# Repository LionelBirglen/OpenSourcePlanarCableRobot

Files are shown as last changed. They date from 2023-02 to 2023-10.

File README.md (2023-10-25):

# Open-Source Planar Cable-Driven Robot

This repository shares all the required information to build and control a simple and low-cost planar cable-driven parallel robot with four actuators, from editable CAD files and programs to electrical circuitry. The robot can be carted and moved around easily. It can also be programmed and operated with an included teach pendant without a computer connected to the machine. Voltages and currents fed to the actuators can be acquired through a D-sub connector for measurements.

See:<br>
http://cctomm.ca/2023/CCToMM_M3_Symposium_paper_9.pdf<br>
for more information. Corresponding citation is:<br>
Design, Control, and Experiments of a Low-Cost Open-Source Planar Cable-Driven Parallel Robot" by Mikael Arslan and Lionel Birglen, 2023 CCToMM M3 Symposium, June 19-20, 2023.

Video demonstrations:<br>
https://www.youtube.com/watch?v=gsjz_0bn3mc<br>
https://www.youtube.com/watch?v=OgFYR7lME20<br>

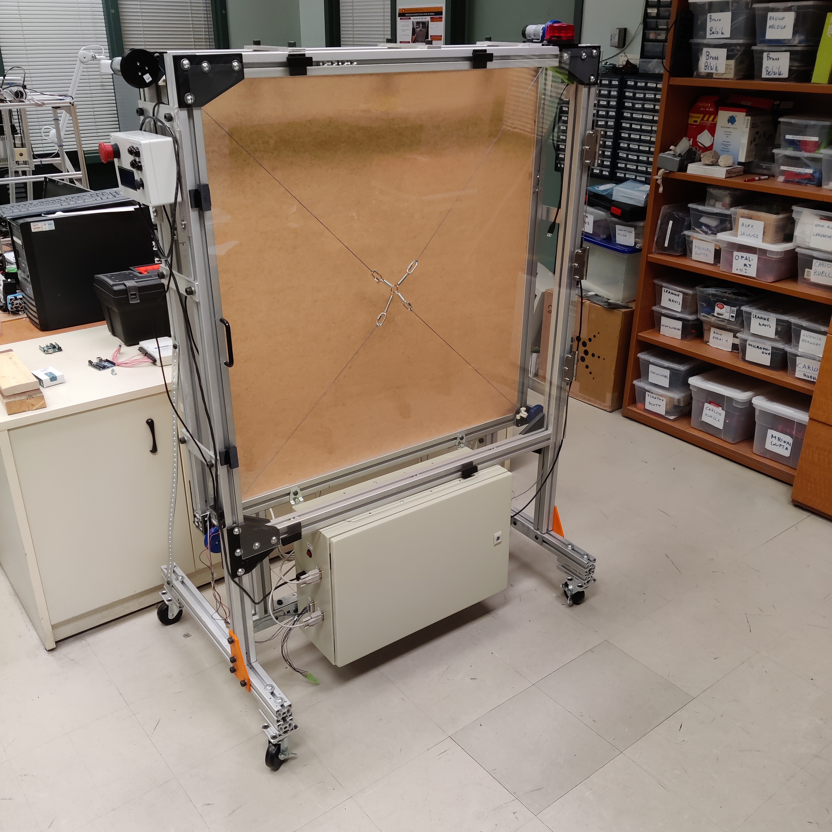
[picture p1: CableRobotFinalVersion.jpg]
Cable Robot Title


All files by Mikael Arslan and Lionel Birglen  <br />
Polytechnique Montreal<br />
2022-...

###  DISCLAIMER:
This hardware and software project is provided "as is", and at your own risk. Under no circumstances shall any author be liable for direct, indirect, special, incidental, or consequential damages resulting from the use, misuse, or inability to use this hardware/software, even if the authors have been advised of the possibility of such damages.

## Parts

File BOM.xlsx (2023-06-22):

PLANAR CDPR BILL OF MATERIALS
Designation | Manufacturer / Supplier | QTY | Unit | Unit Price | Total | Link / Comment
MECHANICAL STRUCTURE
Aluminum extrusions 45mm | Bosh-Rexroth | 14.1 | m | $35.36 | $498.55 | https://store.boschrexroth.com/Assembly-Technology/Basic-mechanic-elements/Profiles-and-accessories/Strut-profile/STRUT-PROFILE_3842553621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
Aluminum bars 3/8" x 1.5" | Hardware store | 1.6 | m | $26.00 | $41.60 | N/A
ABS for 3D printed parts | Amazon | 3.6 | kg | $22.87 | $82.35 | https://www.amazon.ca/AMZ3D-1-75mm-Black-Printer-Filament/dp/B01D999TVO
Caster wheels | Amazon | 4 |  | $6.05 | $24.19 | https://www.amazon.com/GBL-Casters-Castors-Furniture-Workbench/dp/B07KVM276F/
Polycarbonate Sheets: 1/8" (front) and 1/4" (back) thick, 1m square | Polyalto | 2 |  | $125.24 | $250.47 | https://www.polyalto.com/fr/catalogue/produits/polycarbonate-gp-tout-usage
Hinges | Amazon | 3 |  | $2.00 | $6.00 | https://www.amazon.com/Brushed-Interior-Corners-Residential-Hardware/dp/B09T3D2C62/
Springs box | Amazon | 1 |  | $12.01 | $12.01 | https://www.amazon.com/Neiko-50456A-Assortment-Compression-Extension/dp/B000K7M36W/
250lb cable | Amazon | 1 |  | $13.95 | $13.95 | https://www.amazon.com/emma-kites-Braided-Creative-Projects/dp/B01850OST0
Drop in T nuts | Aliexpress | 180 |  | $0.47 | $84.15 | https://www.aliexpress.com/item/4001249847405.html
M8 screws | Aliexpress | 180 |  | $0.31 | $55.44 | https://www.aliexpress.com/item/4000148454577.html
Door handle | Amazon | 1 |  | $6.50 | $6.50 | https://www.amazon.com/Uxcell-a11081400ux0074-Cabinet-Plastic-Rectangular/dp/B007VBT5CA/
Mini carabiner clip kit | Amazon | 1 |  | $8.99 | $8.99 | https://www.amazon.com/Stainless-Steel-Carabiner-Clip-Spring-Snap/dp/B08DTCM52N/
Eye hooks #3 kit | Aliexpress | 1 |  | $2.38 | $2.38 | https://www.aliexpress.com/item/1005002732256168.html
M3 screw kit | Amazon | 1 |  | $17.96 | $17.96 | https://www.amazon.com/VIGRUE-570PCS-Stainless-Assortment-Machine/dp/B08H24W42K/
ELECTRICAL HARDWARE
Panel mount usb connector | Amazon | 1 |  | $7.99 | $7.99 | https://www.amazon.com/ChenYang-Degree-Angled-Female-extension/dp/B00S5WJ5RO/
Electrical cabinet | Allied Electric | 1 |  | $103.46 | $103.46 | https://www.alliedelec.com/product/rs-pro-by-allied/7755328/70824480/
Electrical box (teach pendant) | Digikey | 1 |  | $7.60 | $7.60 | https://www.digikey.com/en/products/detail/bud-industries/PT-11557-G/387082
Push buttons | Digikey | 4 |  | $2.01 | $8.04 | https://www.digikey.com/en/products/detail/e-switch/PS1023ABLK/82862
Potentiometer Joystick | Digikey | 1 |  | $4.50 | $4.50 | https://www.digikey.com/en/products/detail/sparkfun-electronics/COM-09032/
680 ohm resistor | Digikey | 8 |  | $0.10 | $0.80 | https://www.digikey.com/en/products/detail/yageo/CFR-25JT-52-680R/9098651
1 kohm resistor | Digikey | 1 |  | $0.10 | $0.10 | https://www.digikey.com/en/products/detail/yageo/CFR-25JB-52-1K/96
100 nF capacitor | Digikey | 8 |  | $0.33 | $2.64 | https://www.digikey.com/en/products/detail/kemet/C320C104K3R5TA/12701287
22mF 25V capacitor | Digikey | 1 |  | $4.87 | $4.87 | https://www.digikey.com/en/products/detail/nichicon/LLS1E223MELB
LCD screen | Adafruit | 1 |  | $17.95 | $17.95 | https://www.adafruit.com/product/198
Barrier Blocks 2 positions | Digikey | 4 |  | $2.59 | $10.36 | https://www.digikey.com/en/products/detail/te-connectivity-amp-connectors/1546477-2/2284035
Barrier Blocks 4 positions | Digikey | 2 |  | $2.94 | $5.88 | https://www.digikey.com/en/products/detail/te-connectivity-amp-connectors/1546306-4/1277415
General purpose prototype boards | Digikey | 5 |  | $1.59 | $7.95 | https://www.digikey.com/en/products/detail/chip-quik-inc/SBBTH1508-1/5978279
Crimp Connectors | Amazon | 1 |  | $39.99 | $39.99 | https://www.amazon.com/haisstronica-Crimping-Connectors-HS-8327-Electrical/dp/B099W4FVRB/
Straight pin header (0.1" pitch) | Robotshop | 5 |  | $1.61 | $8.05 | https://www.robotshop.com/products/sfe-straight-pin-headers
Power entry module (IEC 320) | Digikey | 1 |  | $1.20 | $1.20 | https://www.digikey.com/en/products/detail/adam-tech/IEC-C-1-150/9830624
DB9 2m cable | Digikey | 4 |  | $5.20 | $20.80 | https://www.digikey.com/en/products/detail/cinch-connectivity-solutions/30-9506-99/3830292
DB-9 female connector | Digikey | 4 |  | $0.70 | $2.80 | https://www.digikey.com/en/products/detail/amphenol-cs-fci/DE09S064TLF/1001839
DB-9 male connector | Digikey | 4 |  | $0.72 | $2.88 | https://www.digikey.com/en/products/detail/amphenol-cs-fci/DE09P064TXLF/1001838
DB-15 | Digikey | 1 |  | $0.75 | $0.75 | https://www.digikey.com/en/products/detail/adam-tech/DA15-PR/9832244
D-sub backshells | Digikey | 4 |  | $0.78 | $3.12 | https://www.digikey.com/en/products/detail/assmann-wsw-components/AGP-09-G/1241839
Power switch on off with light | Digikey | 1 |  | $9.59 | $9.59 | https://www.digikey.com/en/products/detail/bulgin/H8553VBBA3-551W/2747894
Red Led | Digikey | 5 |  | $0.17 | $0.85 | https://www.digikey.com/en/products/detail/creeled-inc/C5SMF-RJF-CT0W0BB1/
CR2032 battery | Digikey | 1 |  | $0.48 | $0.48 | https://www.digikey.com/en/products/detail/murata-electronics/CR2032/9558425
12V Strobe Light | Amazon | 1 |  | $20.49 | $20.49 | https://www.amazon.com/12V-24V-Flashing-Magnetic-Straight-Forklift/dp/B07KF4HJ83/
Emergency Switch | Digikey | 1 |  | $57.77 | $57.77 | https://www.digikey.com/en/products/detail/omron-automation-and-safety/A22E-M-01/456041
Panduct wire duct | Allied Electric | 6 |  | $6.88 | $41.28 | https://www.alliedelec.com/product/panduit/f1x2lg6/70333454/
Power cord | Amazon | 1 |  | $6.75 | $6.75 | https://www.amazon.com/dp/B072BYGKZZ/
Nylon spacer kit | Amazon | 1 |  | $9.99 | $9.99 | https://www.amazon.com/Electrical-Spacers-Assortment-Threaded-Receptacle/dp/B0BKFYFXWR/
PG7 Cable Gland (10pcs) | Aliexpress | 1 |  | $1.17 | $1.17 | https://www.aliexpress.com/item/4000242432947.html
AWG 22 electrical wire (control signals) | Amazon | 1 |  | $16.98 | $16.98 | https://www.amazon.com/Silicone-Electrical-Conductor-Parallel-Flexible/dp/B07K9R9LBV/
AWG 18 electrical wire (motors) | Amazon | 1 |  | $12.98 | $12.98 | https://www.amazon.com/Silicone-Electrical-Conductor-Parallel-Flexible/dp/B07K9R9LBV/
MECHATRONIC ELEMENTS
DC Gearmotor 37Dx73L | Pololu | 4 |  | $51.95 | $207.80 | https://www.pololu.com/product/4755
L-Brackets | Pololu | 2 |  | $9.95 | $19.90 | https://www.pololu.com/product/1084
Universal Hubs | Pololu | 2 |  | $9.95 | $19.90 | https://www.pololu.com/product/1083
Current sensors ACS711EX | Pololu | 4 |  | $3.95 | $15.80 | https://www.pololu.com/product/2452
12V power supply | Digikey | 1 |  | $41.27 | $41.27 | https://www.digikey.com/en/products/detail/mean-well-usa-inc/LRS-350-12/7705030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
Roboclaw solo 30A | BasicMicro | 4 |  | $89.95 | $359.80 | https://www.basicmicro.com/Roboclaw-Solo-30A-34VDC-Motor-Controller_p_44.html
Arduino Mega | Robotshop | 1 |  | $48.40 | $48.40 | https://www.robotshop.com/products/arduino-mega-2560-microcontroller-rev3
Arduino pro mini | Robotshop | 1 |  | $10.95 | $10.95 | https://www.robotshop.com/products/arduino-pro-mini-328-5v-16mhz
VINT Hub (optional) | Phidgets | 1 |  | $30.00 | $30.00 | https://www.phidgets.com/?tier=3&catid=2&pcid=1&prodid=1202
MISC
Labels for the wiring | Amazon | 1 |  | $7.59 | $7.59 | https://www.amazon.com/Mr-Label-Inkjet-Printer-Support-Waterproof/dp/B01HB59G7O/
GRAND TOTAL |  |  |  |  | $2306.01
 |  |  |  |  | All prices exclude VAT, custom duties, and shipping
TOOL LIST
Screwdrivers
Drill with various size meshes
Soldering iron and tin
Miter saw (capable of aluminium cutting)
Allen keys
Electric tape
Heat shrink tubing
Crimping tool (if suggested connector kit not purchased)
Multimeter (optional, debugging)
Oscilloscope (optional, debugging)
Label maker (optional but strongly recommended)
AUTHORS
by Mikael Arslan and Lionel Birglen
Polytechnique Montreal
created: 2023-02-17
last update: 2023-06-22
Rev 1.02

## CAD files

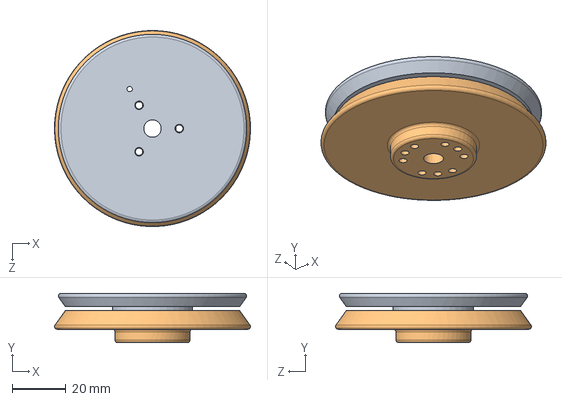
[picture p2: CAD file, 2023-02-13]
CAD/SpiralPulley/Assembly.SLDASM
73.1 x 18.4 x 73.1 mm
partB
partA

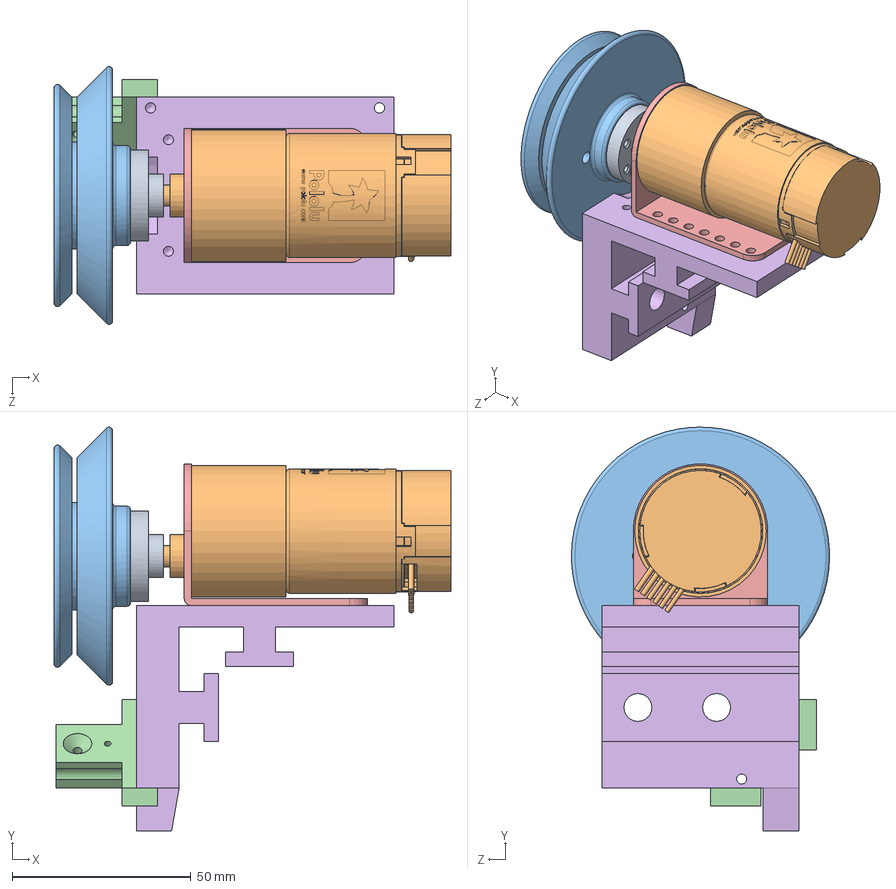
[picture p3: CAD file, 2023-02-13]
CAD/RobotMainFrame/ActuationUnit.SLDASM
111.0 x 112.9 x 72.1 mm
coupleur_poulie-moteur
moteur
poulie_originale
redirecteur
support_moteur
support_moteur_extrusion

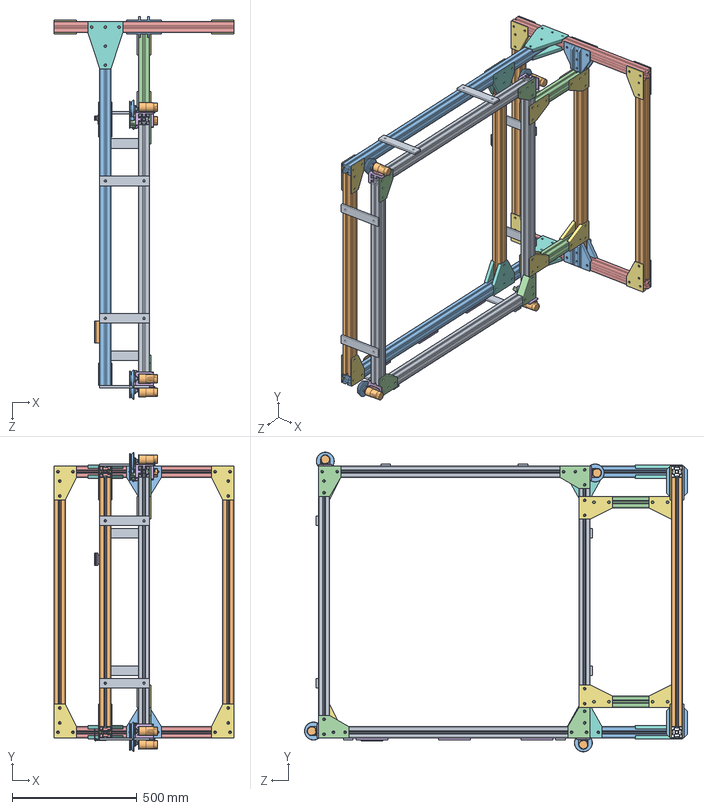
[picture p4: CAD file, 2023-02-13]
CAD/RobotMainFrame/CableRobotMainFrame.SLDASM
720.0 x 1201.8 x 1535.9 mm
extrusion_alu_45_1045 x 4
extrusion_alu_45_1000 x 5
extrusion_alu_45_1415 x 2
extrusion_alu_45_325 x 2
extrusion_alu_45_720 x 2
cale_charnière x 3
equerre_L_support_angle x 10
equerre_T_support_inferieur x 4
coupleur_poulie-moteur x 4
moteur x 4
poulie_originale x 4
redirecteur x 4
support_moteur x 4
support_moteur_extrusion x 4
equerre_L_support_angle_sym x 10
equerre_T_support_milieu x 4
barre_alu x 8
demi_charnière_porte_3.5in x 2
equerre_T_support_base x 4
equerre_L_support_angle_arriere x 4
support_aimant_plexi
support aimant cadre

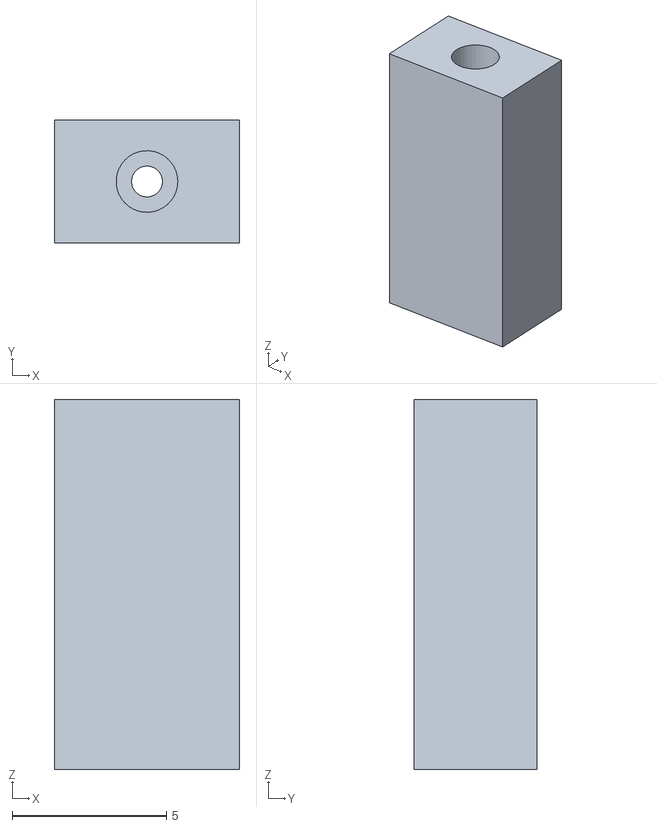
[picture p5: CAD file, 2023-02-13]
CAD/ElectricalCabinet/3DPrintedParts/standoff.STL
6.00 x 4.00 x 12.0

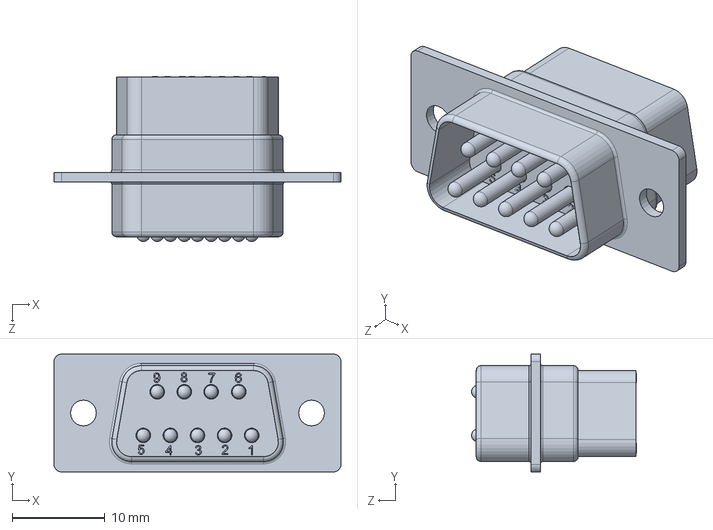
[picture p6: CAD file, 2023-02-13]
CAD/ElectricalCabinet/DB9_pins.SLDPRT
30.9 x 12.7 x 17.8 mm

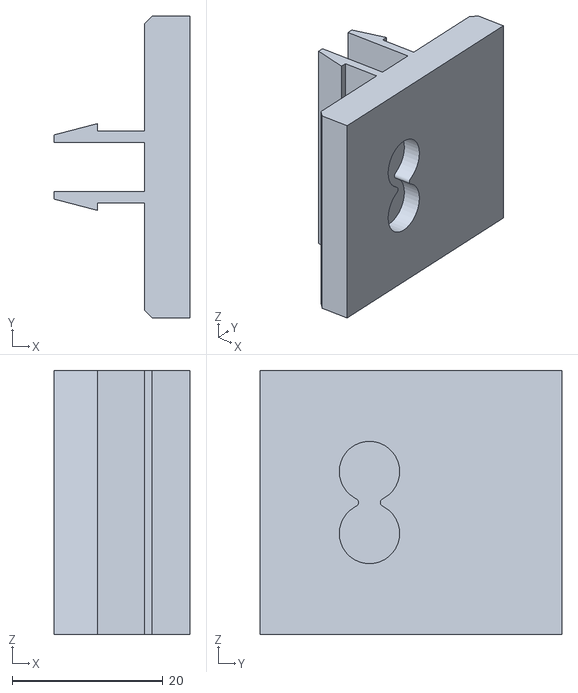
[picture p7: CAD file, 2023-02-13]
CAD/RobotMainFrame/3DPrintedParts/support aimant cadre_0.STL
18.0 x 40.0 x 35.0

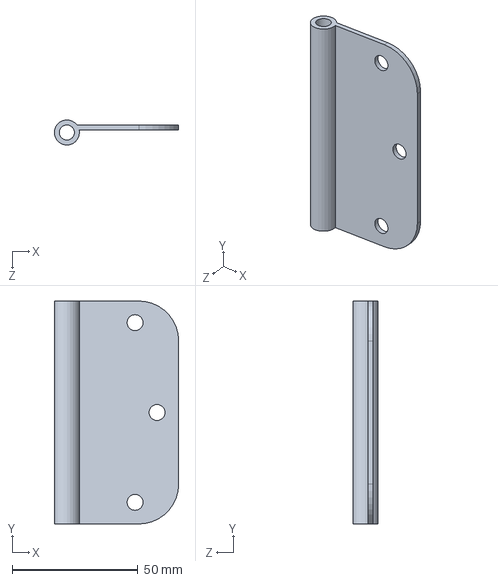
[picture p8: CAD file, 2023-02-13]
CAD/RobotMainFrame/demi_charnière_porte_3.5in.SLDPRT
49.4 x 88.6 x 9.98 mm

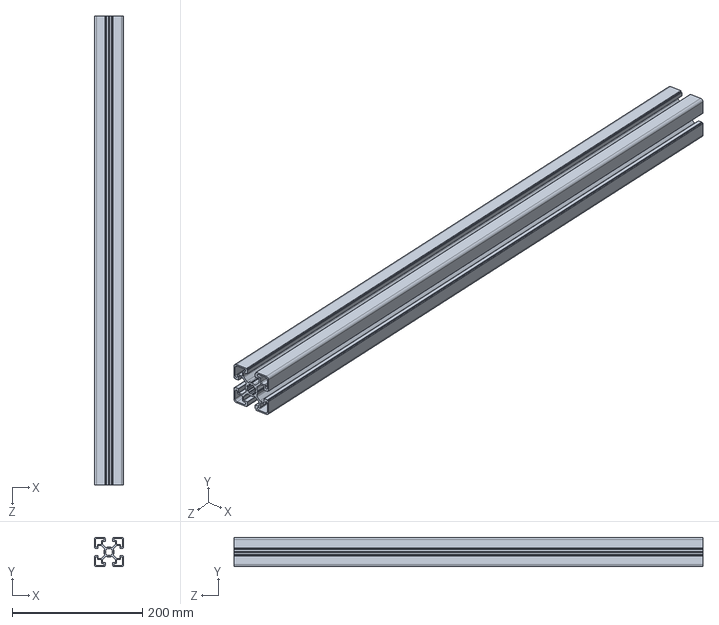
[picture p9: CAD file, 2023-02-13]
CAD/RobotMainFrame/extrusions/extrusion_alu_45_720.SLDPRT
45.0 x 45.0 x 720.0 mm

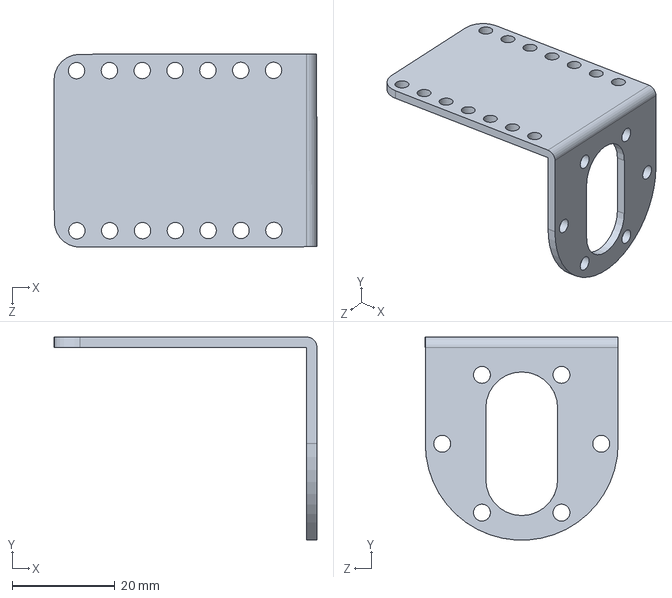
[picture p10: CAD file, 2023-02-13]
CAD/RobotMainFrame/pieces_bloc_moteur/support_moteur.SLDPRT
51.3 x 39.6 x 37.7 mm

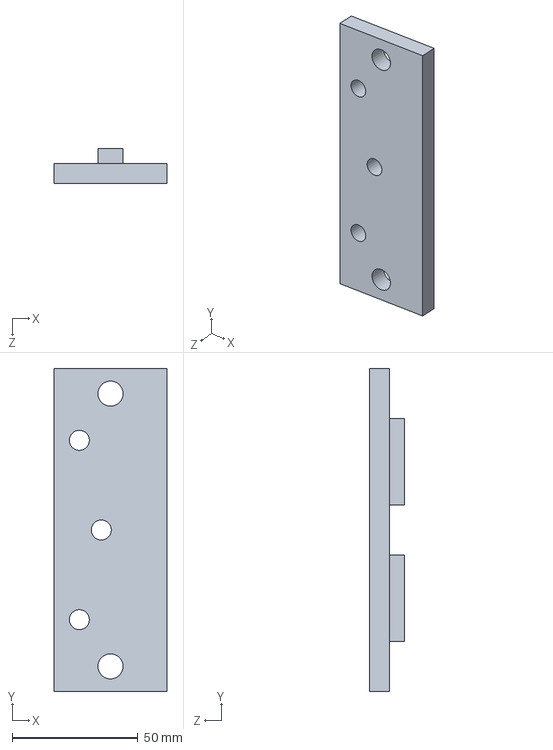
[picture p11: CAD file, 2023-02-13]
CAD/RobotMainFrame/pieces_imprimes/cale_charnière.SLDPRT
45.0 x 128.6 x 14.0 mm

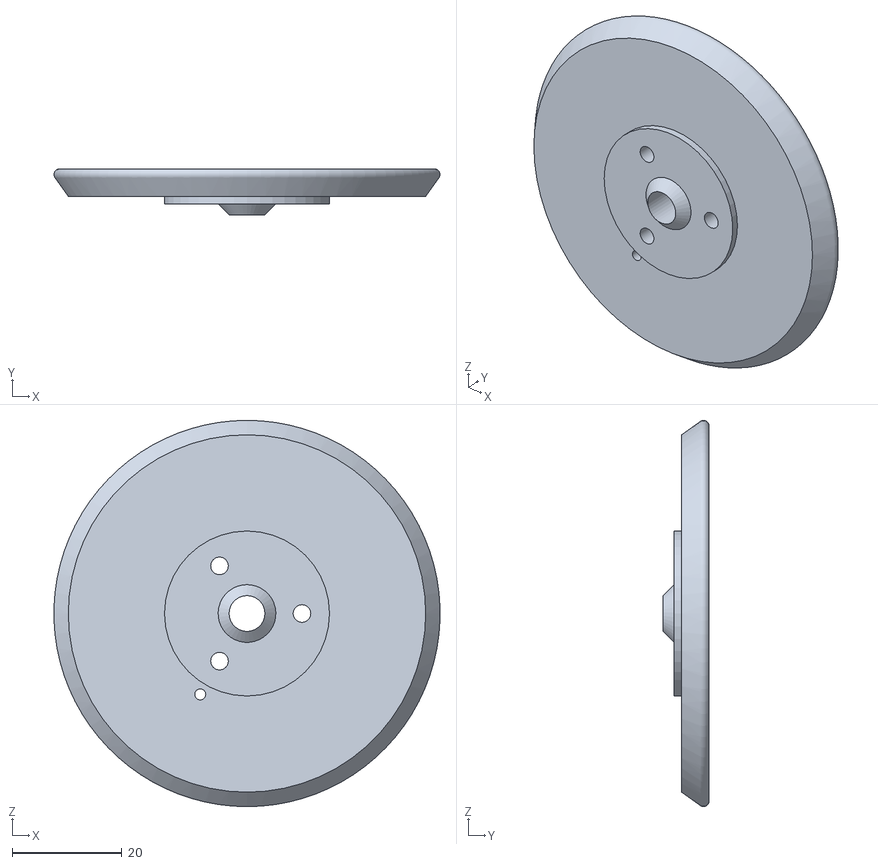
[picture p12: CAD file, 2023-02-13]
CAD/SpiralPulley/3DPrintedParts/partB.STL
70.2 x 8.40 x 70.3

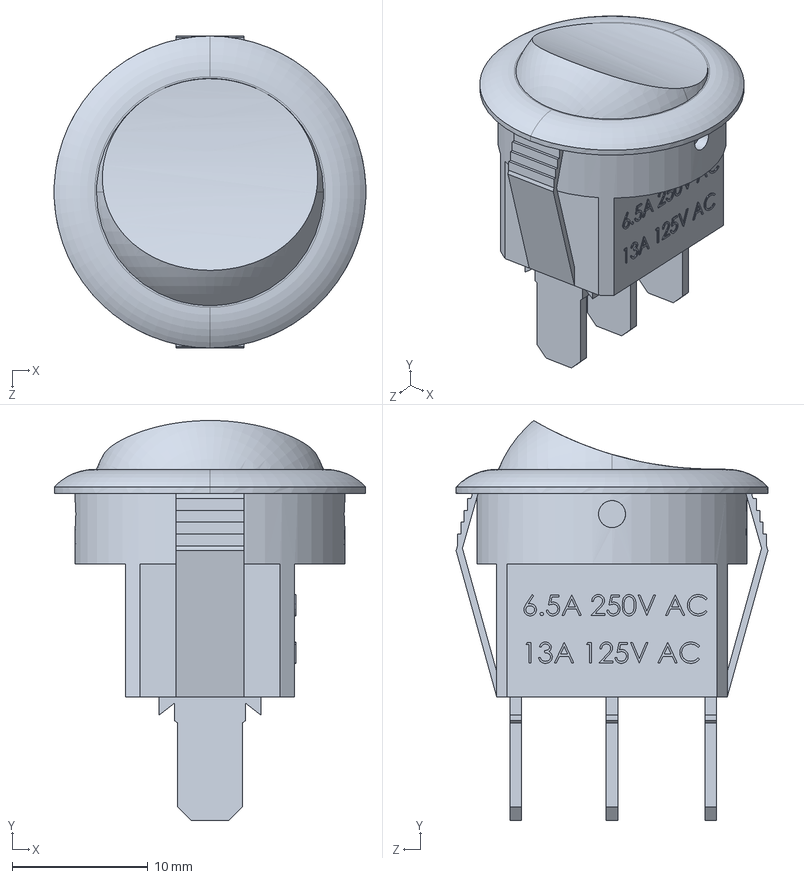
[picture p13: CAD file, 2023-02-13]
CAD/ElectricalCabinet/round_switch.SLDPRT
23.0 x 29.5 x 23.0 mm

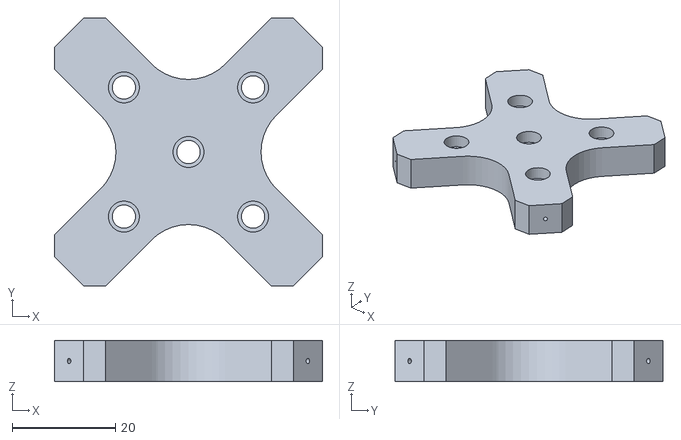
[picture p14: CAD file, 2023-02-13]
CAD/RobotMainFrame/3DPrintedParts/support_led_1.STL
51.9 x 51.9 x 8.00

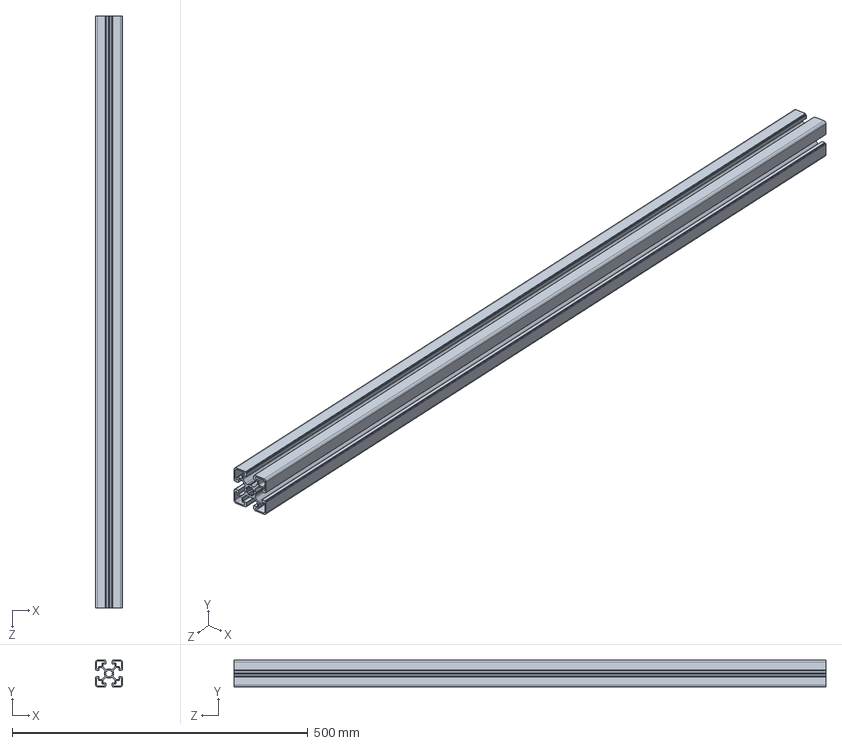
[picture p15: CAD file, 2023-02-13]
CAD/RobotMainFrame/extrusions/extrusion_alu_45_1000.SLDPRT
45.0 x 45.0 x 1000.0 mm

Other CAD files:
CAD/RobotMainFrame/pieces_bloc_moteur/coupleur_poulie-moteur.SLDPRT
CAD/RobotMainFrame/pieces_imprimes/Extrusion45Foot.stp
CAD/SpiralPulley/3DPrintedParts/partA.STL
CAD/SpiralPulley/partA.SLDPRT
CAD/ElectricalCabinet/Mean Well LRS-350 Power Supply.SLDPRT
CAD/ElectricalCabinet/arduino_mega.SLDPRT
CAD/ElectricalCabinet/backboard.SLDPRT
CAD/ElectricalCabinet/bonier_4.SLDPRT
CAD/ElectricalCabinet/bonier_6.SLDPRT
CAD/ElectricalCabinet/bouton.SLDPRT
CAD/ElectricalCabinet/current_sensor_ACS711EX.SLDPRT
CAD/ElectricalCabinet/d-sub-15.SLDPRT
CAD/ElectricalCabinet/roboclaw.SLDPRT
CAD/ElectricalCabinet/standoff_arduino.SLDPRT
CAD/ElectricalCabinet/wire_duct_250.SLDPRT
CAD/ElectricalCabinet/wire_duct_295.SLDPRT
CAD/ElectricalCabinet/wire_duct_440.SLDPRT
CAD/RobotMainFrame/3DPrintedParts/Extrusion45Foot v2_4.STL
CAD/RobotMainFrame/3DPrintedParts/cale_charnière_0.STL
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

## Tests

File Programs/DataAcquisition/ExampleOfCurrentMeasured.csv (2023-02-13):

2.300262451171875000e-03 -2.989200000004021973e-03 -4.746200000003586439e-03 4.461991999999941338e-01 -4.985159999999955183e-02
5.768537521362304688e-03 1.709499999999541942e-02 1.313899999999845747e-02 4.686289999999917466e-01 -3.416540000000911625e-02
1.411795616149902344e-02 4.626840000000020936e-02 3.556880000000317565e-02 5.000013999999939340e-01 -2.793000000006928829e-03
1.553654670715332031e-02 -4.095860000001261270e-02 2.208159999998882128e-02 4.731735999999944209e-01 -3.196640000000461335e-02
3.055453300476074219e-02 3.952479999999303217e-02 5.785199999999290910e-02 5.089439999999914033e-01 -7.337600000009603107e-03
3.854870796203613281e-02 -5.224680000000825331e-02 -5.840180000000261273e-02 3.992872000000022847e-01 -1.035072000000056835e-01
3.854870796203613281e-02 6.415359999999514784e-02 5.785199999999290910e-02 5.133419999999933037e-01 8.348599999995043319e-03
5.453991889953613281e-02 1.944059999999359079e-02 -5.620280000000521525e-02 4.127743999999953228e-01 -8.562200000000363964e-02
6.253337860107421875e-02 3.058219999999556293e-02 6.239659999999558337e-02 5.022003999999913315e-01 -4.992000000004326310e-03
7.054591178894042969e-02 3.754399999988944359e-03 1.997399999996485320e-03 4.618853999999987803e-01 -3.196640000000461335e-02
7.852053642272949219e-02 2.838319999999816545e-02 3.322319999999079343e-02 4.887131999999982934e-01 -9.536600000007000588e-03
7.852053642272949219e-02 6.195459999999775036e-02 3.776779999999346771e-02 5.000013999999939340e-01 -2.793000000006928829e-03
9.450960159301757812e-02 4.172379999999753508e-02 3.776779999999346771e-02 4.843151999999963930e-01 -1.408120000000967487e-02
9.450960159301757812e-02 6.415359999999514784e-02 7.573719999999495300e-02 5.200855999999933754e-01 2.183579999999518684e-02
1.105012893676757812e-01 4.626840000000020936e-02 2.428059999999332419e-02 4.708279999999962495e-01 -2.522280000001164701e-02
1.184952259063720703e-01 5.960899999999247356e-02 6.239659999999558337e-02 5.089439999999914033e-01 6.149599999997645838e-03
1.184952259063720703e-01 2.603759999999288866e-02 2.647959999999782710e-02 4.775715999999963213e-01 -2.522280000001164701e-02
1.344830989837646484e-01 4.846739999999050141e-02 4.671039999999093695e-02 5.043993999999958344e-01 -2.793000000006928829e-03
1.424777507781982422e-01 3.058219999999556293e-02 2.882519999998889304e-02 4.731735999999944209e-01 -3.856340000000391122e-02
1.505122184753417969e-01 6.195459999999775036e-02 6.459559999999298086e-02 5.000013999999939340e-01 3.950599999993142930e-03
1.505122184753417969e-01 3.058219999999556293e-02 2.647959999999782710e-02 4.843151999999963930e-01 -2.522280000001164701e-02
1.664774417877197266e-01 6.855159999999704823e-02 6.239659999999558337e-02 5.089439999999914033e-01 1.289319999999061217e-02
1.744587421417236328e-01 5.953399999993447267e-03 2.882519999998889304e-02 4.753725999999918184e-01 -3.196640000000461335e-02
1.744587421417236328e-01 5.301199999999317569e-02 6.005099999999741200e-02 5.065984000000003373e-01 3.950599999993142930e-03
1.904482841491699219e-01 -5.188200000008524881e-03 3.102419999999339595e-02 4.731735999999944209e-01 -2.742180000000193907e-02
1.984767913818359375e-01 7.089719999999521960e-02 5.110839999999283734e-02 4.976557999999957627e-01 -4.992000000004326310e-03
2.064363956451416016e-01 -5.188200000008524881e-03 1.313899999999845747e-02 4.574873999999897745e-01 -3.856340000000391122e-02
2.064363956451416016e-01 6.195459999999775036e-02 5.785199999999290910e-02 5.022003999999913315e-01 -2.793000000006928829e-03
2.224295139312744141e-01 -3.436160000000620940e-02 -3.482000000016860497e-04 4.350575999999921617e-01 -4.310800000000658549e-02
2.224295139312744141e-01 7.089719999999521960e-02 6.005099999999741200e-02 5.089439999999914033e-01 1.054759999999244080e-02
2.384200096130371094e-01 1.709499999999541942e-02 6.395399999998385709e-03 4.461991999999941338e-01 -5.879420000000412649e-02
2.464241981506347656e-01 4.406939999999570645e-02 4.671039999999093695e-02 5.000013999999939340e-01 -4.992000000004326310e-03
2.544059753417968750e-01 1.489599999999091651e-02 -6.968999999999825334e-02 3.948891999999932789e-01 -9.001999999999843460e-02
2.623970508575439453e-01 4.406939999999570645e-02 5.565299999998840619e-02 5.089439999999914033e-01 1.604999999994971560e-03
2.704010009765625000e-01 5.066639999999500432e-02 2.882519999998889304e-02 4.372565999999895592e-01 -5.644859999999884970e-02
2.783887386322021484e-01 1.709499999999541942e-02 4.216579999999536810e-02 4.843151999999963930e-01 -1.628020000000707235e-02
2.864050865173339844e-01 5.960899999999247356e-02 3.556880000000317565e-02 4.954567999999983652e-01 -1.035072000000056835e-01
2.864050865173339844e-01 2.603759999999288866e-02 5.110839999999283734e-02 4.976557999999957627e-01 -4.992000000004326310e-03
2.944121360778808594e-01 5.960899999999247356e-02 4.451140000000064489e-02 5.022003999999913315e-01 -5.940000000024259208e-04
3.063070774078369141e-01 -7.672900000000248966e-02 -8.757520000000029725e-02 3.768573999999975666e-01 -1.213924000000077275e-01
3.086130619049072266e-01 3.754399999988944359e-03 8.594399999995783190e-03 4.552883999999923770e-01 -4.310800000000658549e-02
3.106274604797363281e-01 1.489599999999091651e-02 2.428059999999332419e-02 4.708279999999962495e-01 -2.962079999999933655e-02
3.186266422271728516e-01 5.960899999999247356e-02 5.565299999998840619e-02 5.089439999999914033e-01 1.289319999999061217e-02
3.186266422271728516e-01 2.838319999999816545e-02 2.208159999998882128e-02 4.731735999999944209e-01 -2.302380000000714411e-02
3.346164226531982422e-01 4.626840000000020936e-02 4.451140000000064489e-02 4.932577999999938623e-01 -5.940000000024259208e-04
3.426268100738525391e-01 2.838319999999816545e-02 2.882519999998889304e-02 4.775715999999963213e-01 -2.522280000001164701e-02
3.426268100738525391e-01 5.960899999999247356e-02 6.005099999999741200e-02 5.065984000000003373e-01 1.729119999999961799e-02
3.586006164550781250e-01 2.383859999999549117e-02 2.428059999999332419e-02 4.664299999999943491e-01 -2.962079999999933655e-02
3.665955066680908203e-01 5.960899999999247356e-02 6.679459999999037834e-02 5.089439999999914033e-01 6.149599999997645838e-03
3.745942115783691406e-01 2.163959999999098827e-02 2.647959999999782710e-02 4.731735999999944209e-01 -2.742180000000193907e-02
3.825850486755371094e-01 6.195459999999775036e-02 6.459559999999298086e-02 5.111429999999959062e-01 1.509219999999511508e-02
3.825850486755371094e-01 -8.567160000000706432e-02 -1.054604000000023412e-01 3.567731999999910197e-01 -1.438222000000053402e-01
3.985764980316162109e-01 3.754399999988944359e-03 1.093999999999395456e-02 4.618853999999987803e-01 -4.310800000000658549e-02
3.985764980316162109e-01 -7.672900000000248966e-02 -9.431880000000747444e-02 3.702603999999982687e-01 -1.347329999999999917e-01
4.145622253417968750e-01 -2.761800000000613764e-02 -3.157400000000309959e-02 4.149733999999998257e-01 -8.342299999999913673e-02
4.225575923919677734e-01 -8.567160000000706432e-02 -1.009158000000067723e-01 3.523751999999962248e-01 -1.438222000000053402e-01
4.225575923919677734e-01 3.512679999999823721e-02 3.322319999999079343e-02 4.775715999999963213e-01 -1.847919999999736440e-02
4.385488033294677734e-01 -7.672900000000248966e-02 -1.032614000000049437e-01 3.567731999999910197e-01 -1.347329999999999917e-01
4.465403556823730469e-01 3.278119999999296041e-02 2.882519999998889304e-02 4.843151999999963930e-01 -2.522280000001164701e-02
4.545538425445556641e-01 -5.188200000008524881e-03 -6.074740000000078410e-02 3.903445999999977101e-01 -8.107740000000096536e-02
4.625315666198730469e-01 4.846739999999050141e-02 5.345399999999811413e-02 5.043993999999958344e-01 1.604999999994971560e-03
4.625315666198730469e-01 4.406939999999570645e-02 -4.051660000000767425e-02 4.239159999999972950e-01 -1.168478000000050532e-01
4.705355167388916016e-01 4.406939999999570645e-02 6.005099999999741200e-02 5.043993999999958344e-01 1.054759999999244080e-02
4.865350723266601562e-01 1.489599999999091651e-02 1.533799999999585495e-02 4.708279999999962495e-01 -2.742180000000193907e-02
4.945104122161865234e-01 3.952479999999303217e-02 5.110839999999283734e-02 4.932577999999938623e-01 3.950599999993142930e-03
5.025124549865722656e-01 7.309619999999972251e-02 6.459559999999298086e-02 5.133419999999933037e-01 2.623379999999708723e-02
5.104999542236328125e-01 3.058219999999556293e-02 4.216579999999536810e-02 4.865141999999937905e-01 -7.337600000009603107e-03
5.184977054595947266e-01 6.635259999999254532e-02 5.110839999999283734e-02 4.976557999999957627e-01 -5.940000000024259208e-04
5.264906883239746094e-01 2.163959999999098827e-02 4.216579999999536810e-02 4.797705999999937188e-01 -1.408120000000967487e-02
5.345206260681152344e-01 5.740999999999507608e-02 5.565299999998840619e-02 4.954567999999983652e-01 -4.992000000004326310e-03
5.425224304199218750e-01 3.512679999999823721e-02 3.322319999999079343e-02 4.686289999999917466e-01 -2.522280000001164701e-02
5.475902557373046875e-01 3.058219999999556293e-02 1.533799999999585495e-02 4.731735999999944209e-01 -3.196640000000461335e-02
5.486729145050048828e-01 2.838319999999816545e-02 2.208159999998882128e-02 4.775715999999963213e-01 -2.962079999999933655e-02
5.497503280639648438e-01 3.952479999999303217e-02 3.322319999999079343e-02 4.753725999999918184e-01 -2.742180000000193907e-02
5.517749786376953125e-01 3.732579999999563469e-02 3.556880000000317565e-02 4.932577999999938623e-01 -1.408120000000967487e-02
5.528295040130615234e-01 3.732579999999563469e-02 3.776779999999346771e-02 4.797705999999937188e-01 -1.628020000000707235e-02
5.538613796234130859e-01 -3.201600000000803803e-02 -3.391960000000127096e-02 4.239159999999972950e-01 -1.235914000000051249e-01
5.559298992156982422e-01 -8.127360000000516393e-02 -9.431880000000747444e-02 3.613177999999936940e-01 -1.303350000000051967e-01
5.570199489593505859e-01 -7.453000000000509218e-02 -7.408800000000725916e-02 3.679147999999929919e-01 -1.281360000000006938e-01
5.580401420593261719e-01 -2.527240000000086084e-02 -2.483040000000302783e-02 4.014861999999925768e-01 -9.676360000000561179e-02
5.590980052947998047e-01 -5.224680000000825331e-02 -5.840180000000261273e-02 3.613177999999936940e-01 -1.392776000000026659e-01
5.603177547454833984e-01 -8.127360000000516393e-02 -7.628700000000465664e-02 3.857999999999950358e-01 -1.079052000000004785e-01
5.623862743377685547e-01 -3.875960000000810979e-02 -5.180480000000331486e-02 4.440001999999967364e-01 -4.530699999999687755e-02
5.623862743377685547e-01 -2.989200000004021973e-03 3.322319999999079343e-02 4.797705999999937188e-01 -2.522280000001164701e-02
5.634076595306396484e-01 3.952479999999303217e-02 3.322319999999079343e-02 4.753725999999918184e-01 -2.522280000001164701e-02
5.644259452819824219e-01 3.952479999999303217e-02 3.102419999999339595e-02 4.708279999999962495e-01 -2.522280000001164701e-02
5.664587020874023438e-01 2.838319999999816545e-02 2.882519999998889304e-02 4.642309999999898462e-01 -2.522280000001164701e-02
5.674738883972167969e-01 3.278119999999296041e-02 1.988259999999142380e-02 4.775715999999963213e-01 -1.628020000000707235e-02
5.685033798217773438e-01 3.058219999999556293e-02 2.647959999999782710e-02 4.731735999999944209e-01 -1.408120000000967487e-02
5.695266723632812500e-01 3.512679999999823721e-02 -6.945200000008089347e-03 4.440001999999967364e-01 -5.879420000000412649e-02
5.705511569976806641e-01 -7.013200000000319179e-02 -7.628700000000465664e-02 3.857999999999950358e-01 -1.146488000000076557e-01
5.716249942779541016e-01 -8.567160000000706432e-02 -1.054604000000023412e-01 3.567731999999910197e-01 -1.347329999999999917e-01
5.726549625396728516e-01 -8.347260000000256142e-02 -1.054604000000023412e-01 3.523751999999962248e-01 -1.414766000000071688e-01
5.727074146270751953e-01 -6.338840000000312003e-02 -7.408800000000725916e-02 3.702603999999982687e-01 -1.213924000000077275e-01
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

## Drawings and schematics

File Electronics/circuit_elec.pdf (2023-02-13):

NKC electronics... | 2.2k

Terminal block...

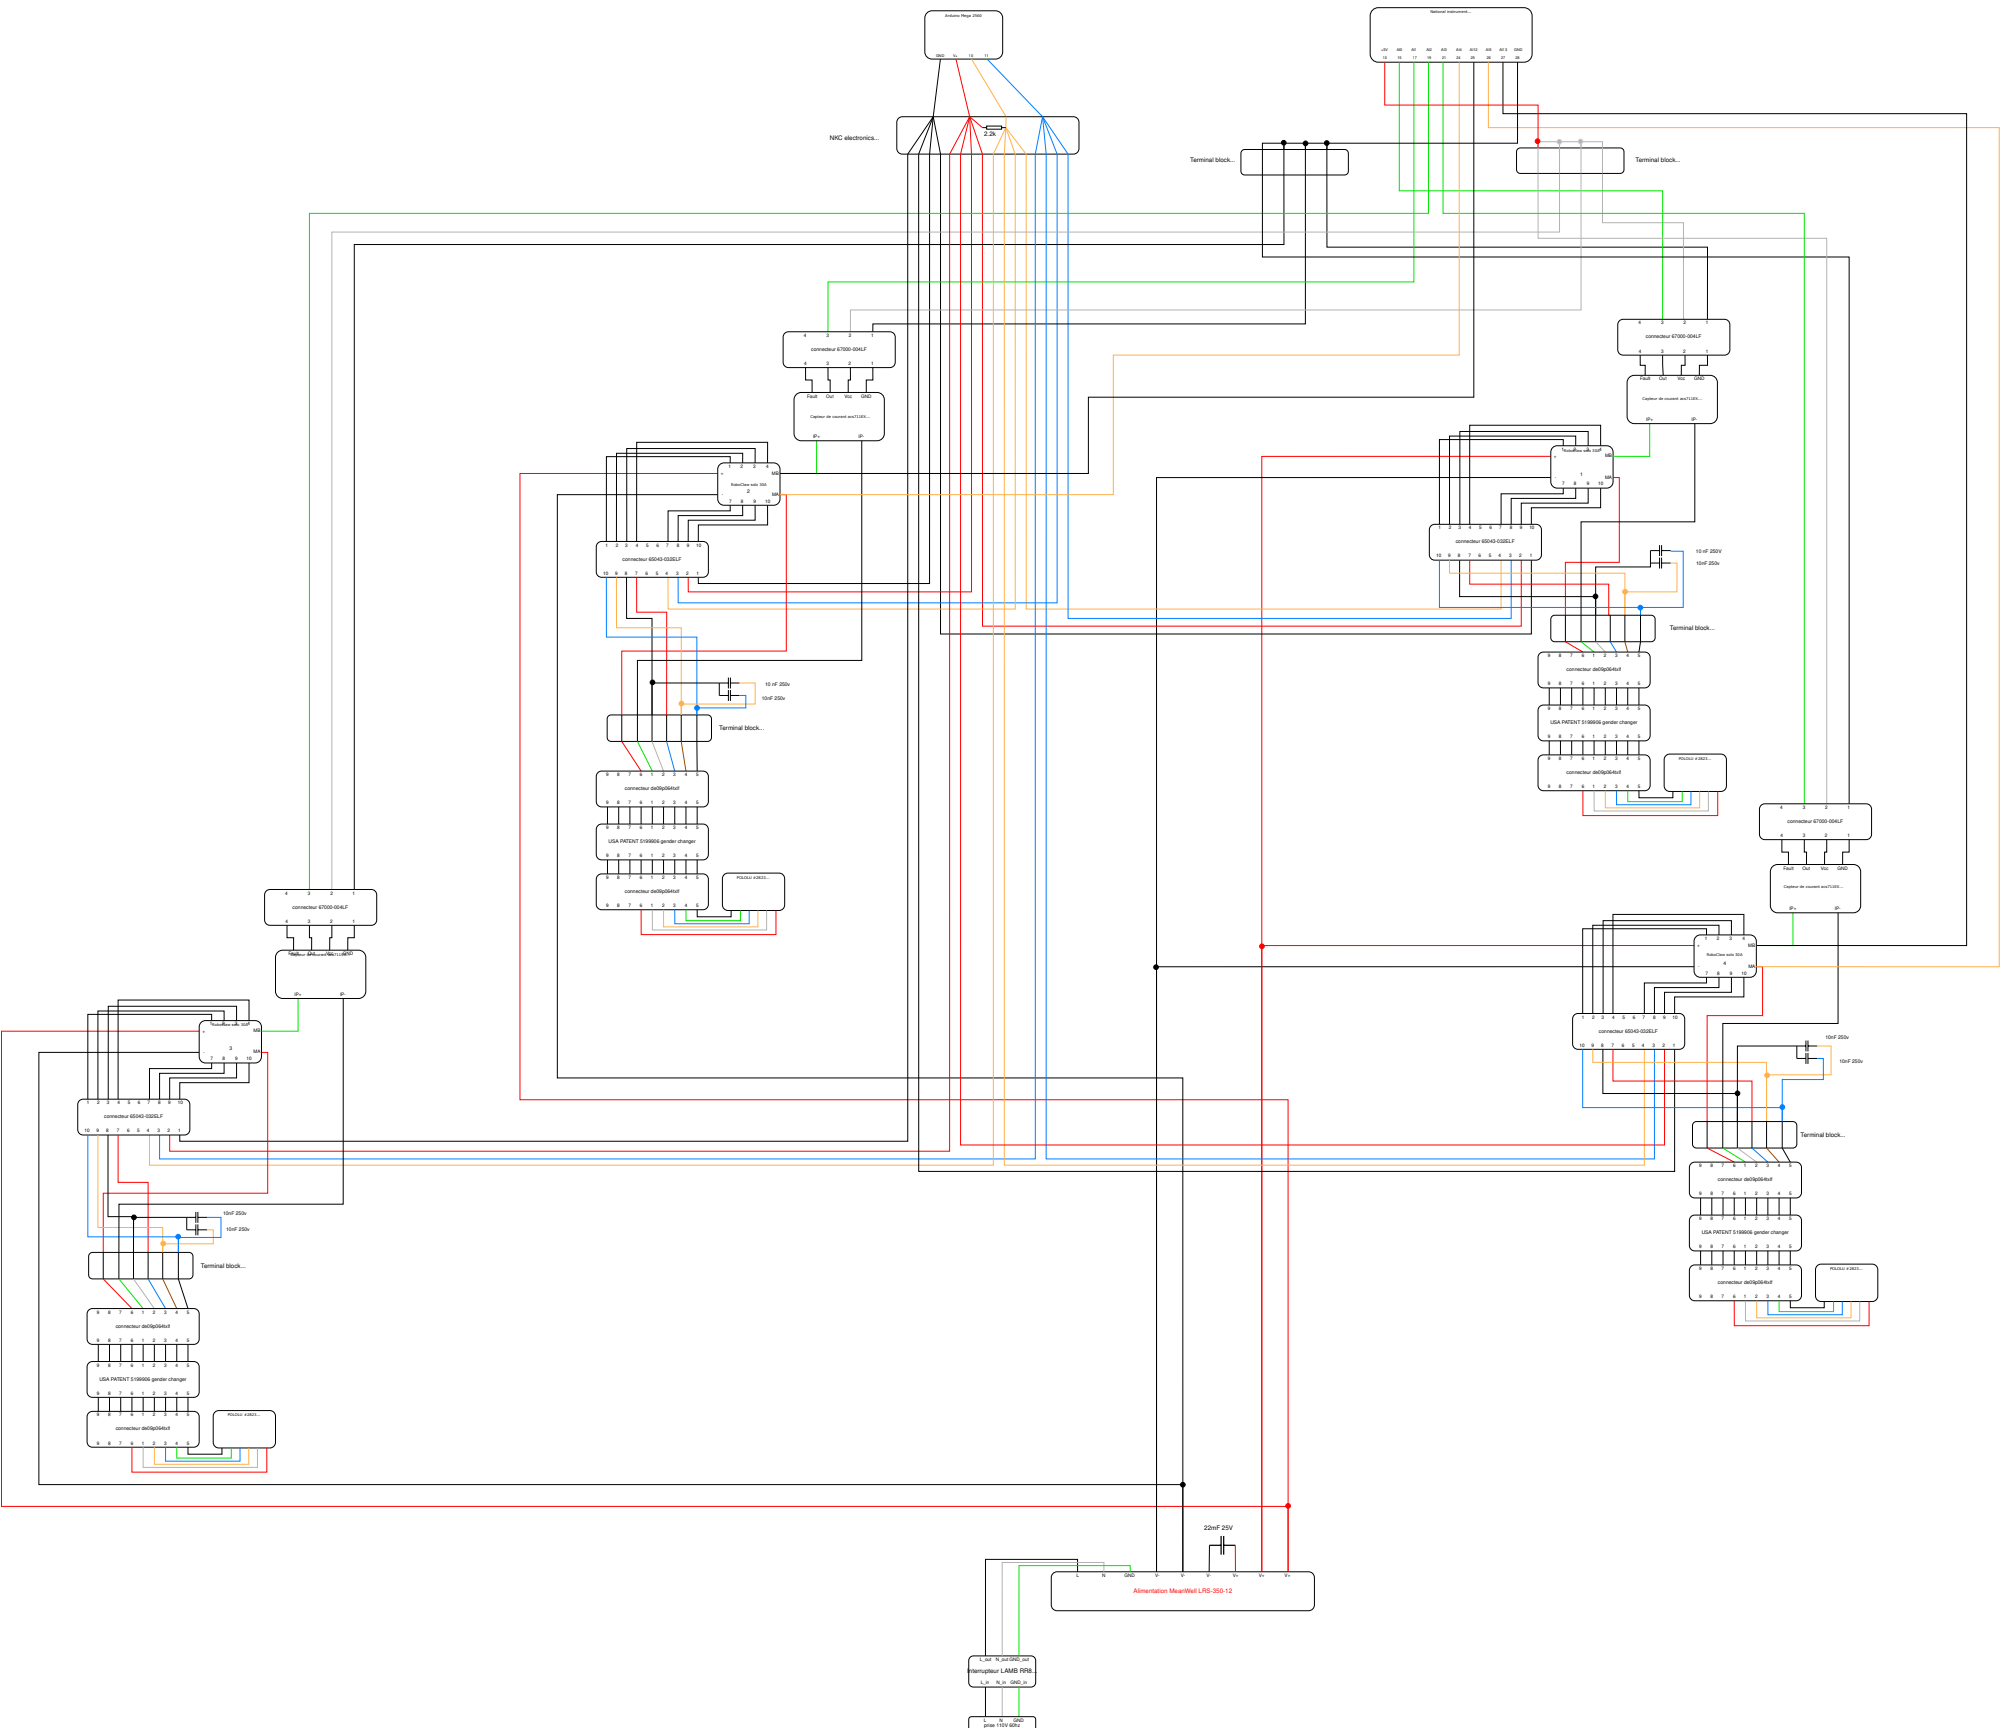
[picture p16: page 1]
Interrupteur LAMB RR8...; L_out; GND_outN_out; GND_inN_in; National instrument...; GND; Arduino Mega 2560; GNDN; prise 110V 60hz; RoboClaw solo 30A; connecteur 65043-032ELF; connecteur 67000-004LF; Fault; VccOut; Terminal block...; POLOLU #2823...; connecteur de09p064txlf

Capteur de courant acs711EX...

USA PATENT 5199906 gender changer

Alimentation MeanWell LRS-350-12

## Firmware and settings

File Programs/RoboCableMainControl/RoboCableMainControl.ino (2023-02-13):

//Includes required to use Roboclaw library
#include <SoftwareSerial.h>
#include "RoboClaw.h"
#include "menu_funcs.h"
#include "variables.h"
#include "com.h"

/*
int step_counter = 0;
int char_step_counter;
char step_msg[50];
int32_t step_mot[4] = {0,0,0,0};
bool read_step = false;

bool decode_step_msg() {

  if (Serial.available()) { // if there is a char

    char step_ch = Serial.read(); // read

    if(step_ch == 'g'){
      Serial.println("zero");
      go_to_zero();
    } 

    if (read_step) { // if we are currently reading a message, add the char to the message
      step_msg[char_step_counter] = step_ch;
      char_step_counter++; // move to the next letter of the message
    }

    if (step_ch == '[') { // if the char read is '#' it means it is the start of a message
      read_step = true; // we set the state as currently reading
      //for (int k = 0; k < msg_length-1; k++)
      
      step_msg[0] = '\0'; // we 'delete' the previous message by inserting an end of line char at the beginning
    }


    else if (step_ch == ']') { // if char = '%' then we reached the end of the message
      step_msg[char_step_counter - 1] = '\0'; // we set the end of the message with end of line char
      char_step_counter = 0; // we reset the position
      read_step = false; // we are no longer reading
      return true; // return true to say that a message has been received
    }
  }

  return false; // no message has been received
}

void mot_step(){
  if(decode_step_msg()){
    String msg = step_msg;

    int current_step = 0;
    int last_i = 0;
    for(int i = 0; i < msg.length(); i++){
      if(msg[i] == ';'){
        step_mot[current_step] = msg.substring(last_i,i).toInt();
        Serial.print(step_mot[current_step]);Serial.print(" ");
        last_i = i+1;
        current_step++;
      }
    }
    Serial.println("\n");

    int cspeed = 5000;
    ismoving = true;
    roboclaw.SpeedAccelDeccelPositionM1(addressM1, RCaccel, cspeed, RCdecel, step_mot[0], buffer_flag);
    roboclaw.SpeedAccelDeccelPositionM1(addressM2, RCaccel, cspeed, RCdecel, step_mot[1], buffer_flag);
    roboclaw.SpeedAccelDeccelPositionM1(addressM3, RCaccel, cspeed, RCdecel, step_mot[2], buffer_flag);
    roboclaw.SpeedAccelDeccelPositionM1(addressM4, RCaccel, cspeed, RCdecel, step_mot[3], buffer_flag);
    RCpos1 = step_mot[0];
    RCpos2 = step_mot[1];
    RCpos3 = step_mot[2];
    RCpos4 = step_mot[3];
  }
}
*/

//This is the first function arduino runs on reset/power up
void setup() {

  Serial.begin(57600); // serial with computer
  Serial1.begin(9600); // communication with slave arduino pro mini
  roboclaw.begin(38400); //Open Serial and roboclaw at 38400bps

  Serial.println("Starting...");
  delay(100);

  test_controllers();

  initialise_com();
  
  zero_software();
  zero_hardware();
  def_L0(); 

}

void loop() {

  //mot_step();

  if(read_serial())
    decode_msg(); // listening to the pro mini
}

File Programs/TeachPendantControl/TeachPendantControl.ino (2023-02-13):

#include "com.h"

long t0 = millis();

void setup() {
  // put your setup code here, to run once:
  Serial.begin(9600);
  pinMode(button_left, INPUT_PULLUP);
  pinMode(button_right, INPUT_PULLUP);
  pinMode(button_gtz, INPUT_PULLUP);
  pinMode(button_sz, INPUT_PULLUP);
  
  lcd.begin(20,4); // Initializes the interface to the LCD screen, and specifies the dimensions (width and height) of the display }
  analogWrite(contrast,20); // Generate PWM signal at pin D11, value of 100 (out of 255)

  initialise_com();  // initialisation
}


void loop() {

  if(read_serial()){ // if we receive the init message we execute the protocole again
    if(strcmp(serial_msg, "init") == 0){
      initialise_com();
      screen_update = true;
      clear_data();
    }
  }

  if(read_button_gtz()){ // if the go to zero button is pressed 
    Serial.println("#gtz%"); // sending the command to the mega
    
    lcd.clear(); // displaying a message on screen
    lcd.setCursor(0, 0);
    lcd.print("going to position");
    lcd.setCursor(0, 1);
    lcd.print("zero");
    //delay(3000);

    serial_msg[0] = '\0';
    while (strcmp(serial_msg, "end_gtz") != 0) // waiting for the end confirmation
      read_serial();

    screen_update = true; // if true, thescreen will be updated prevents flickering
    clear_data();
  }

  else if(read_button_sz()){ // if set zero button pressed
    Serial.println("#sz%"); // sending command
    lcd.clear(); // displaying
    lcd.setCursor(0, 0);
    lcd.print("setting position");
    lcd.setCursor(0, 1);
    lcd.print("zero");
    delay(3000);
    screen_update = true;
    clear_data();
  }

  update_screen(); // updating the screen if necessary

  if(!mode_selected) // if the mode is not selected
    select_mode();
  
  else{ // else execute the selected mode

    switch(mode){
      case 0:
        step_by_step_mode();
        break;
      case 1:
        auto_mode();
        break;
      case 2:
        auto_interp_mode();
        break;
      case 3:
        manual_mode();
        break;
      default:
        mode_selected = false;
        break;
    }

  }

  
}

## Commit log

2023-02-20 Add files via upload
    Added v1.0 of BOM
    [BOM.xlsx]
2023-02-21 Add files via upload
    added label maker
    [BOM.xlsx]
2023-06-22 Add files via upload
    Updated BOM to include drill
    [BOM.xlsx]
